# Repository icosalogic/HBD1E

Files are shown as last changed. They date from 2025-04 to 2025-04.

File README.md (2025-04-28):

# HBD1E
Kicad project for a configurable gate driver board to drive two MOSFETs with TO-247-4 package and
pinout [Drain, Source, KelvinSource, Gate].

Front side of board:

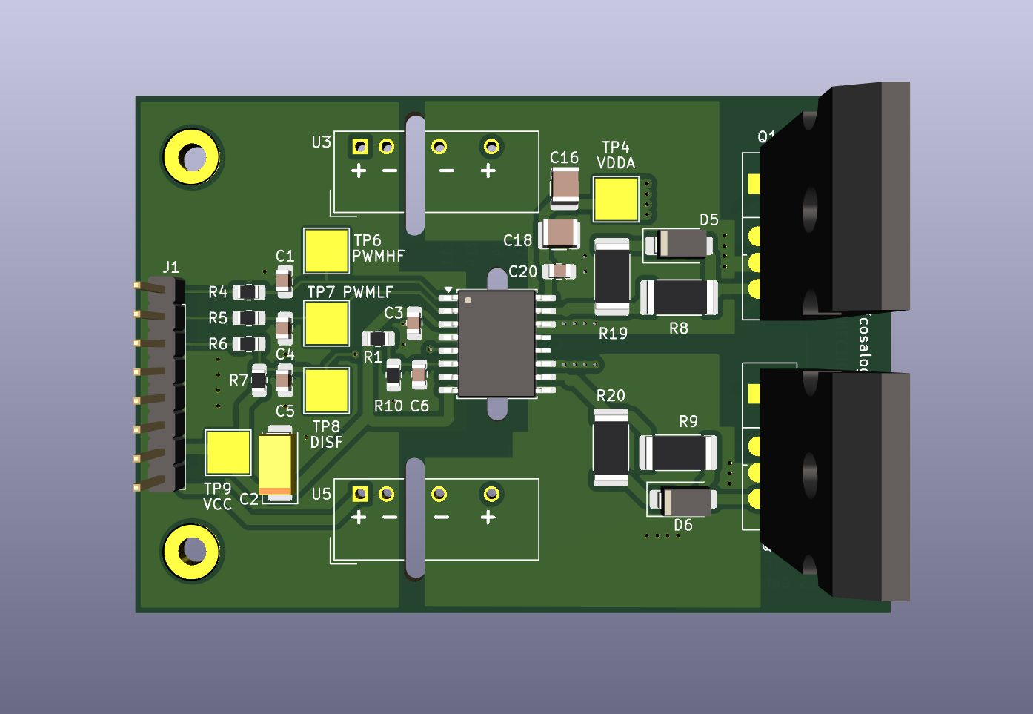
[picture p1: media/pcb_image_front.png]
Image front of PCB


Back side of board:

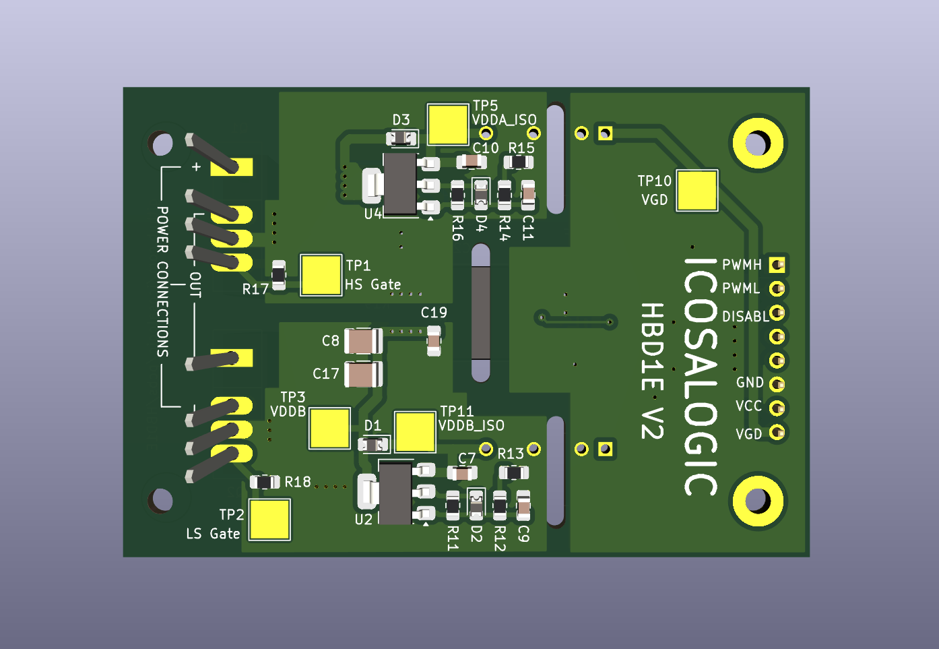
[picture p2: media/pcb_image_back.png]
Image back of PCB


# Features

- Supports 2 independent channels with 1 MOSFET per channel.
- No high-power connections on the board.  The user is free to connect the MOSFET power pins in any configuration they wish.
- Utilizes a gate driver chip in an SOIC-16 wide package, with a pin layout supported by multiple vendors.
- Each channel can be independently configured to be isolated from the gate driver control circuit.
- Each channel can be independently configured to use a linear regulator to precisely control the gate driver voltage.
- Most compatible gate driver chips support configurable dead time.

# Applications

- Half bridge, with input and output having a common ground: Configure the high side to be isolated, and the
low side non-isolated.
- T-Type inverter leg: Use 2 boards, with all gate power domains isolated, with the two middle MOSFETs configured
appropriately for common drain or common source.
- High power parallel MOSFETs: Disable dead time on the gate driver chip, and configure both MOSFET power
domains as non-isolated.

# Board Connections

Board input pins:  

Board input pins

- PWMH: PWM signal for the high-side MOSFET Q1, uses typical CMOS switching levels (off <= 0.8V, on >= 2.0V).
- PWML: PWM signal for the low-side MOSFET Q2, uses typical CMOS switching levels.
- DISABL: Pull this value low to enable the driver chip.  There is a pull up resistor to VCC on this circuit,
so the control component must pull this signal low to enable switching.  Uses typical CMOS switching levels.
- GND: Ground common to VCC and VGD.
- VCC: Power to the control side of the gate driver chip.  Typically 3.3V or 5V, maximum 20V.
- VGD: Power to the gate driver regions, optionally through isolation modules.

For the reference gate driver chip UCC21520, VCC and VGD may be the same for applications with lower
gate voltages.  Or you may choose to have them be separate, and use a higher voltage VGD to gain headroom
through the isolated modules, and configure the linear regulators to provide a precise post-isolation
gate drive voltage.

Note that there are no on-board connections for the high-current drain and source pins for either
MOSFET Q1 or Q2.  These must be connected separately, either through appropriately-sized wires or
a properly-designed laminated bus.

# Schematic

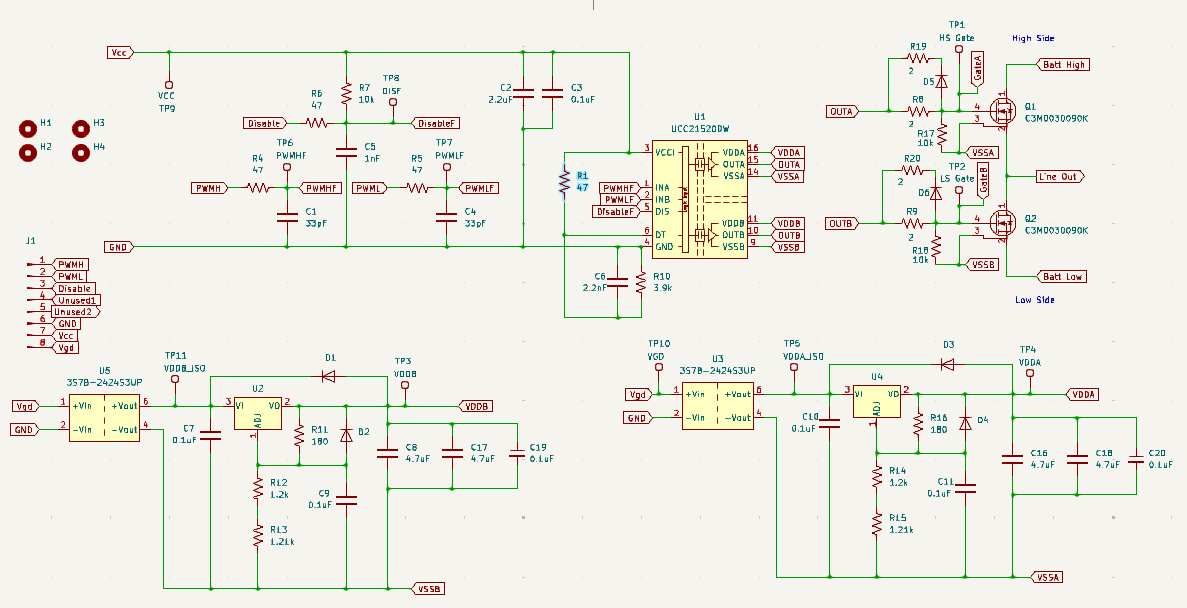
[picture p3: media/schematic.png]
Schematic drawing


# PCB Layout Details

PCB components:

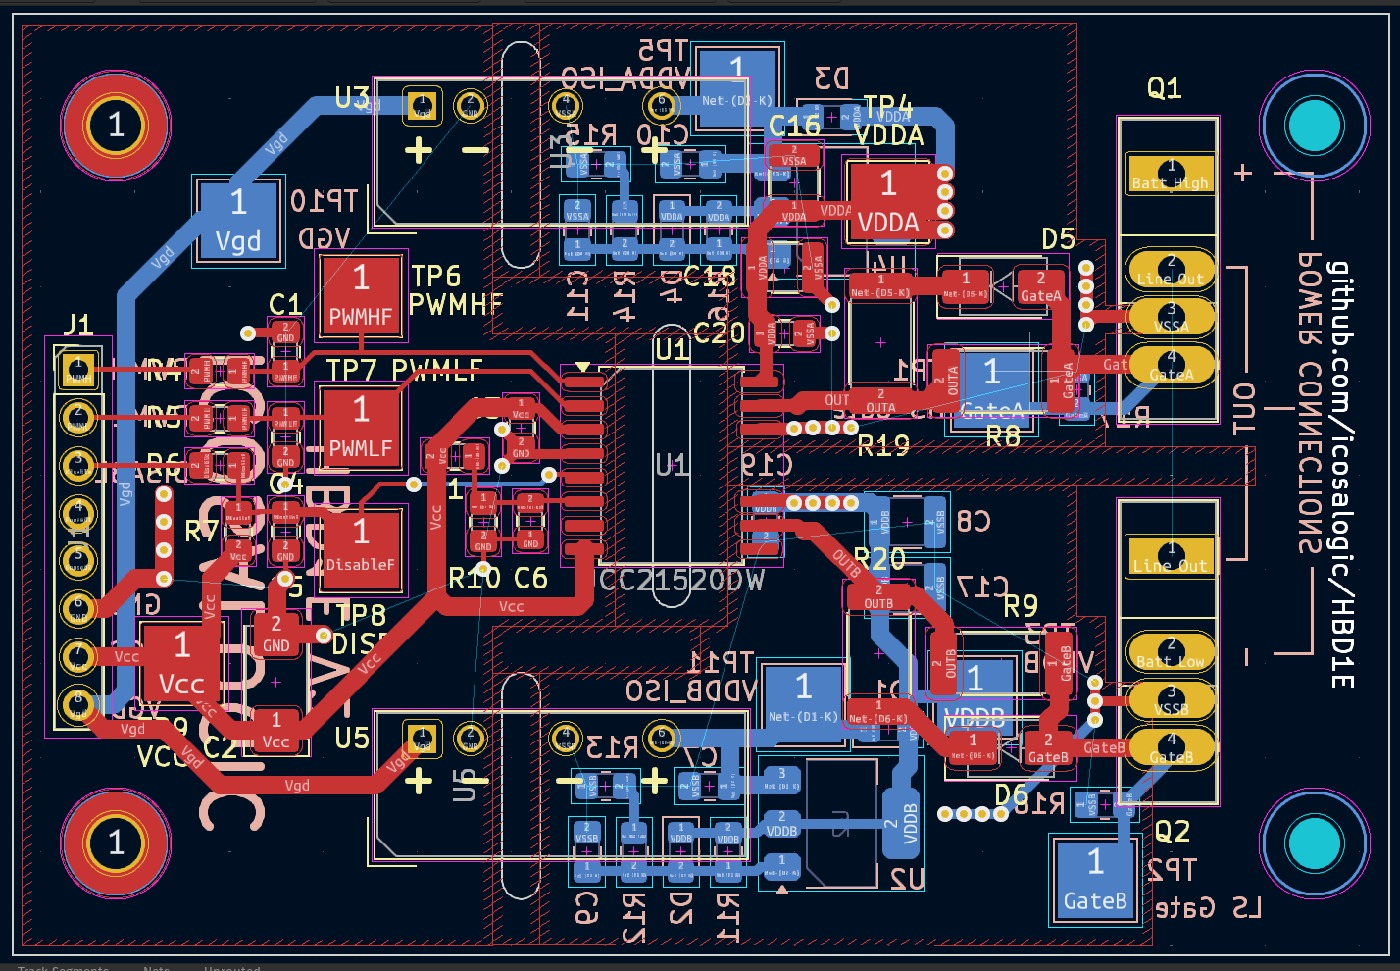
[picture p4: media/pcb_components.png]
PCB components


Front copper layer:

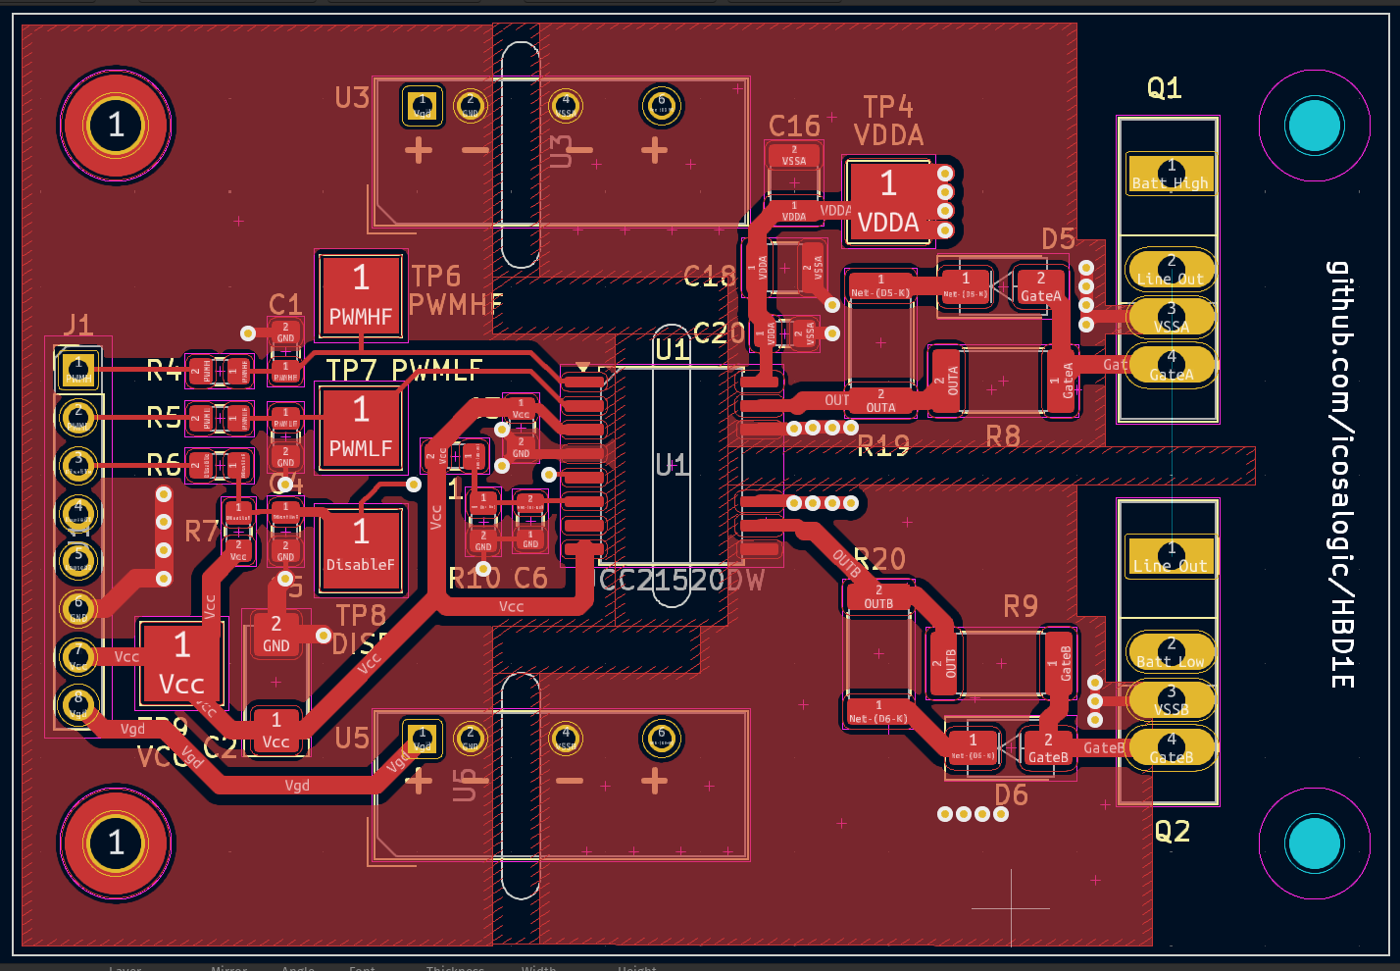
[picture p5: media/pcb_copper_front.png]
PCB front copper layer


Back copper layer:

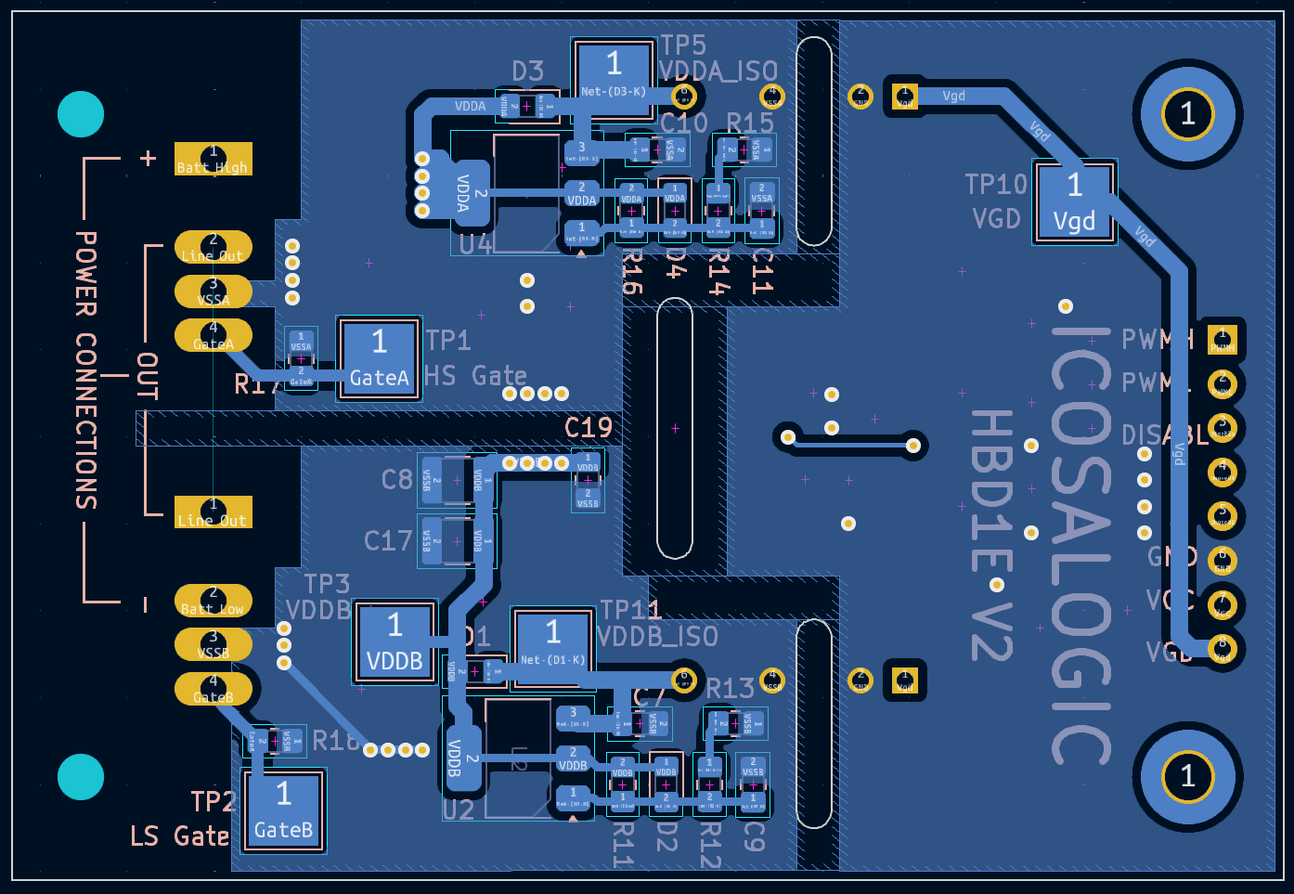
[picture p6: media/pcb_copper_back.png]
PCB back copper layer


# Configuring Channel Isolation

The front of the board has marked locations for two DC-DC isolated modules, U3 (high side, shown below) and U5 (low side).

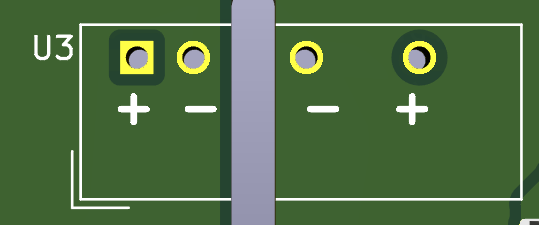
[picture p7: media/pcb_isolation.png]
Isolated module marking
  

These modules take power from the VGD pin, and supply it to the regions of the PCB driving the gates for
the high side MOSFET Q1 and the low side MOSFET Q2.

To make either region isolated, solder a DC-DC isolated converter module in the marked location.
Our test boards used a Gaptec 3S7B-2424S3UP, but pin-compatible 7-SIP components are available from multiple manufacturers.

To make one of these power domains non-isolated, solder a wire connection from + to + and another from - to -.
Ordinary AWG 20 gauge hookup wire is adequate.

# Configuring Gate Drive Voltage Regulation

On the back side of the board, under the isolated modules U3 and U5, are locations for LM317 linear regulators
and associated components.

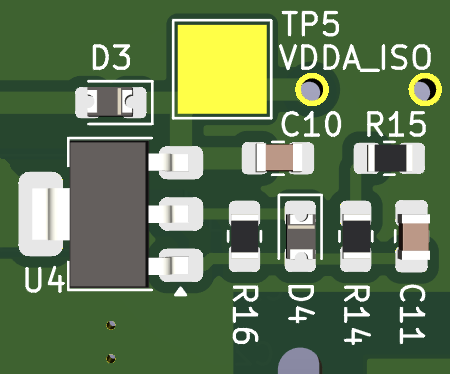
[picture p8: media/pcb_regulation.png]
Gate drive voltage regulation
  

- High Side: (under U3) U4, D3, D4, C10, C11, R14, R15, R16
- Low Side: (under U5) U2, D1, D2, C7, C9, R11, R12, R13

The following table shows which resistors on this board map to those in a typical LM317 datasheet.
This should allow you to select resistor values to configure your desired gate driver voltage.

| Datasheet | High Side | Low Side |
| --- | --- | --- |
| R1 | R16 | R11 |
| R2 |  R14+R15  | R12+R13  |

Note that we used 2 resistors in series for the R2 resistor from the datasheet.
The power dissipation from the minimum regulation current may exceed the limit for a typical
1/10 watt resistor, so we use 2 resistors in series to spread the thermal load.

Here is a table showing combinations for some typical gate drive voltages, using common resistor values.
Of course, more precise voltages can be obtained using more specific resistor values and higher
tolerance 0.1% resistors.

| Target Voltage | R16/R11 | R14+R15/R12+R13 | Computed Voltage |
| --- | --- | --- | --- |
| 10 | 180 | 270/1000 | 10.069 |
| 12 | 180 | 560/1000 | 12.083 |
| 15 | 180 | 1000/1000 | 15.139 |
| 18 | 180 | 1200/1200 | 17.917 |
| 20 | 180 | 1200/1500 | 20.000 |

Note also that the LM317 is a very robust device that may not require all the configured components.
The adjust capacitors may be omitted if your testing shows that ripple and other voltage transients
do not cause any downstream issues when switching the MOSFETs.
Each of the adjust capacitors is paired with a diode:

- C9, D2
- C11, D4

If you omit the adjust capacitor, you can also omit the matching diode.  If you use the adjust capacitor,
you should also use the diode to prevent the capacitor from discharging through the regulator in a power off
scenario.

Also note that you should always populate D1 and D3, since there are large capacitors for the gate driver
chip that may discharge through the regulator in a power off scenario.  D1 and D3 will prevent this.

To configure either the high-side or low-side power domain for voltage regulation, populate the associated
components as listed above.

To configure either of the power domains without voltage regulation, omit all of the regulation components
listed above for that domain, and replace the associated diode (D1 or D3) with a 0 ohm shunt resistor.

# Configuring Dead Time

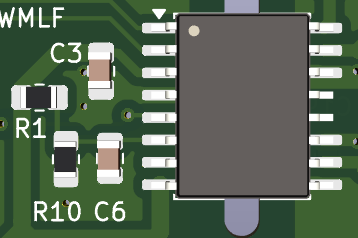
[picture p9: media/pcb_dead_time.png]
Dead time configuration
  

The components used to configure dead time are R1, R10 and C6.

Some, but not all of the pin-compatible gate driver chips support controlling dead time between Q1 and Q2
gate transitions, using a resistor connected to pin 6.  If the gate driver chip you use does not support dead
time generation, then do not populate R1, R10 and C6, and ignore the rest of this section.

If your gate driver chip supports dead time insertion, populate R10 and optionally C6 according to the
datasheet for your chip.  Do not populate R1.

If your chip supports dead time insertion, but you wish to suppress it, populate R1, but not R10 and C6.
This may be desireable if you use this board in a high-current parallel MOSFET application, where you want
both MOSFETs on at the same time.

If your control logic providing the PWM signals also implements dead time, one strategy is to program an
absolute minimum dead time via the hardware as described in this section, and program an optimized, longer
dead time in your control logic.  The gate driver chip uses the longer of the hardware configured dead
time or the software-controlled dead time in the PWM inputs.

# Configuring Input Signal Filtering

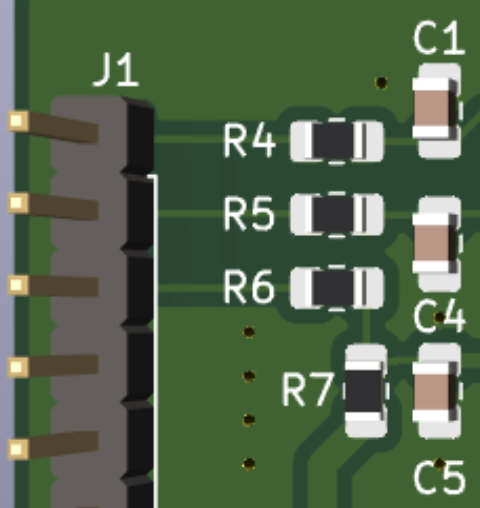
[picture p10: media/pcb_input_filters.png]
Input signal filter configuration


Each of the 3 input signals from the controller to this gate driver board has an RC circuit to
filter transients that may cause issues for the gate driver IC input logic.  These signals and the
associated filter components are listed below.

| Signal Name | Filter Resistor | Value | Capacitor | Value | Pull Up Resistor | Value |
| --- | --- | ----- | --- | ----- | --- | ----- |
| PWMH | R4 |  47Ω | C1 |  33pF | | |
| PWML | R5 |  47Ω | C4 |  33pF | | |
| DISABL | R6 |  47Ω | C5 | 1nF | R7 |  10k  |

The size of all these components is 0805, making them less trouble to hand solder while changing
filter components.

# Test Points

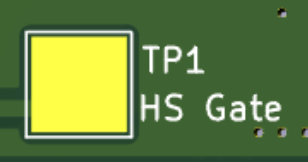
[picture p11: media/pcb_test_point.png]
Test points


There are numerous test points located on both sides of the board to which users can solder
surface mount test point loops, for example KOA Speer RCWCTE.
This gives you the ability to clip oscilloscope leads to enable monitoring various signals while
debugging the gate driver configuration.

### Caution!  This board may use high voltages that are hazardous to humans.
- Be very careful when connecting test leads to potentially high voltage points on the circuit board.
- High voltages may also break test equipment if proper grounding and isolation practices are not followed.
- Please be careful!

List of test points on the board:
| Label |  Name | Location | Description |
| ----- | --- | --- | --- |
| TP1 | HS Gate  | Bottom | High side MOSFET gate pin |
| TP2 | LS Gate  | Bottom | Low side MOSFET gate pin |
| TP3 | VDDB | Bottom | Low side post-regulated gate driver voltage |
| TP4 | VDDA | Top | High side post-regulated gate driver voltage |
| TP5 | VDDA_ISO | Bottom | High side post-isolation, pre-regulated voltage |
| TP6 | PWMHF | Top | High side post-filter PWM input signal |
| TP7 | PWMLF | Top | Low side post-filter PWM input signal |
| TP8 | DISF | Top | Disable post-filter input signal |
| TP9 | VCC | Top | Logic side power for gate driver chip |
| TP10  | VGD | Bottom | Pre-isolation gate driver voltage |
| TP11  | VDDB_ISO | Bottom | Low side post-isolation, pre-regulated voltage  |

# Reference Components

- Gate driver chip: Texas Instruments UCC21520
- MOSFET: Infineon AIMZH120R020M1TXKSA1
- Isolated DC-DC module: Gaptec 3S7B-2424S3UP
- Linear Regulator: Texas Instruments LM317

# Example Bill of Materials (BOM)

An example BOM is located in the file HBD1E_BOM.csv.

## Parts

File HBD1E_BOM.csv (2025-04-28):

Id | Designator | Footprint | Quantity | Designation | Supplier and ref
1 | TP4 | TestPoint_Pad_4.0x4.0mm | 1 | VDDA
2 | H2,H1 | MountingHole_2.7mm_M2.5_Pad_TopBottom | 2 | MountingHole
3 | Q1,Q2 | TO-247-4_Vertical | 2 | C3M0030090K
4 | C5 | C_0805_2012Metric_Pad1.18x1.45mm_HandSolder | 1 | 1nF
5 | C2 | CP_EIA-6032-20_AVX-F_Pad2.25x2.35mm_HandSolder | 1 | 2.2uF
6 | R6,R5,R1,R4 | R_0805_2012Metric_Pad1.20x1.40mm_HandSolder | 4 | 47
7 | D5,D6 | D_SMA | 2 | US1B
8 | TP9 | TestPoint_Pad_4.0x4.0mm | 1 | VCC
9 | TP6 | TestPoint_Pad_4.0x4.0mm | 1 | PWMHF
10 | R9,R19,R20,R8 | R_2512_6332Metric_Pad1.40x3.35mm_HandSolder | 4 | 2
11 | TP7 | TestPoint_Pad_4.0x4.0mm | 1 | PWMLF
12 | C1,C4 | C_0805_2012Metric_Pad1.18x1.45mm_HandSolder | 2 | 33pF
13 | C6 | C_0805_2012Metric | 1 | 2.2nF
14 | U5,U3 | Converter_DCDC_TRACO_TBA2-xxxx_Single_THT | 2 | 3S7B-2424S3UP
15 | R10 | R_0805_2012Metric_Pad1.20x1.40mm_HandSolder | 1 | 3.9k
16 | C3,C20,C9,C10,C7,C19,C11 | C_0805_2012Metric_Pad1.18x1.45mm_HandSolder | 7 | 0.1uF
17 | C16,C18,C17,C8 | C_1210_3225Metric | 4 | 4.7uF
18 | H4,H3 | MountingHole_2.7mm | 2 | MountingHole
19 | J1 | PinHeader_1x08_P2.54mm_Vertical | 1 | Conn_01x08_Male
20 | U1 | SOIC-16W_7.5x10.3mm_P1.27mm_no_pins_12_13 | 1 | UCC21520DW
21 | R7,R17,R18 | R_0805_2012Metric_Pad1.20x1.40mm_HandSolder | 3 | 10k
22 | TP8 | TestPoint_Pad_4.0x4.0mm | 1 | DISF
23 | TP2 | TestPoint_Pad_4.0x4.0mm | 1 | LS Gate
24 | TP1 | TestPoint_Pad_4.0x4.0mm | 1 | HS Gate
25 | R11,R16 | R_0805_2012Metric_Pad1.20x1.40mm_HandSolder | 2 | 180
26 | R14,R12 | R_0805_2012Metric_Pad1.20x1.40mm_HandSolder | 2 | 1.2k
27 | R13,R15 | R_0805_2012Metric_Pad1.20x1.40mm_HandSolder | 2 | 1.21k
28 | U2,U4 | SOT-223-3_TabPin2 | 2 | LM317_SOT-223
29 | D4,D1,D3,D2 | D_0805_2012Metric_Pad1.15x1.40mm_HandSolder | 4 | US1B
30 | TP10 | TestPoint_Pad_4.0x4.0mm | 1 | VGD
31 | TP5 | TestPoint_Pad_4.0x4.0mm | 1 | VDDA_ISO
32 | TP3 | TestPoint_Pad_4.0x4.0mm | 1 | VDDB
33 | TP11 | TestPoint_Pad_4.0x4.0mm | 1 | VDDB_ISO

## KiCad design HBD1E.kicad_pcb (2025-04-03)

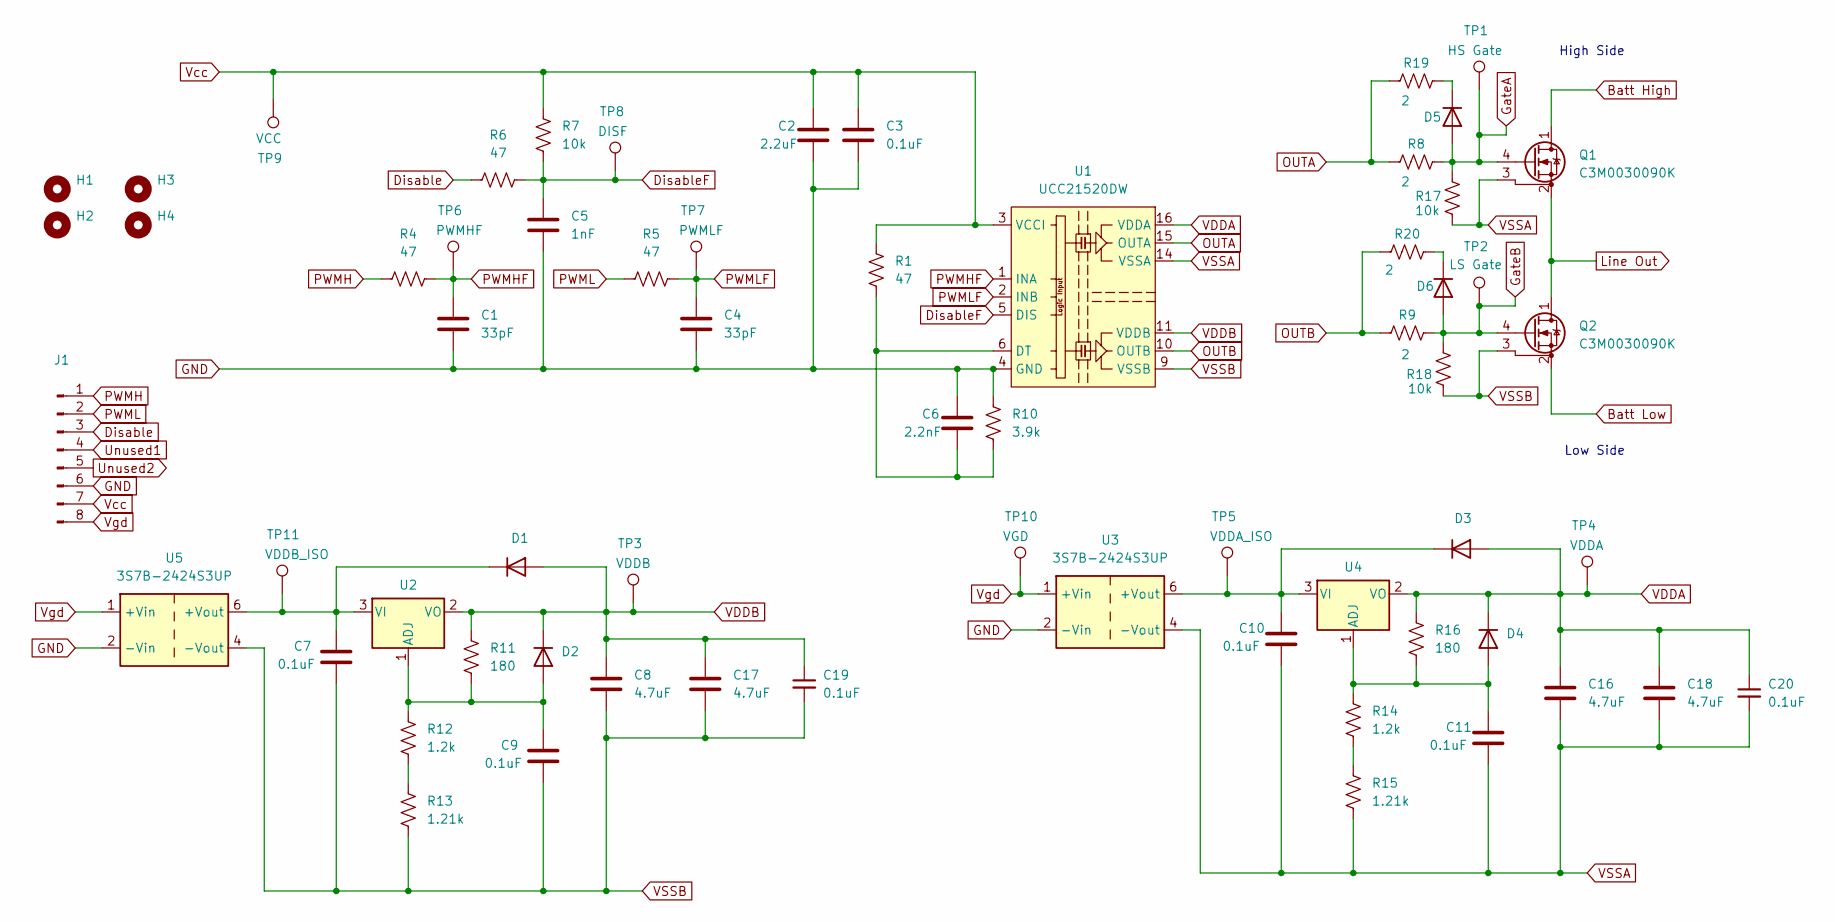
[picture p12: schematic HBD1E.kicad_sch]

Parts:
C1, C4: 33pF; C_0805_2012Metric_Pad1.18x1.45mm_HandSolder
C2: 2.2uF; CP_EIA-6032-20_AVX-F_Pad2.25x2.35mm_HandSolder
C3, C7, C9, C10, C11, C19, C20: 0.1uF; C_0805_2012Metric_Pad1.18x1.45mm_HandSolder
C5: 1nF; C_0805_2012Metric_Pad1.18x1.45mm_HandSolder
C6: 2.2nF; C_0805_2012Metric
C8, C16, C17, C18: 4.7uF; C_1210_3225Metric
D1, D2, D3, D4: US1B; D_0805_2012Metric_Pad1.15x1.40mm_HandSolder
D5, D6: US1B; D_SMA
H1, H2: MountingHole; MountingHole_2.7mm_M2.5_Pad_TopBottom
H3, H4: MountingHole; MountingHole_2.7mm
J1: Conn_01x08_Male; PinHeader_1x08_P2.54mm_Vertical
Q1, Q2: C3M0030090K; TO-247-4_Vertical
R1, R4, R5, R6: 47; R_0805_2012Metric_Pad1.20x1.40mm_HandSolder
R7, R17, R18: 10k; R_0805_2012Metric_Pad1.20x1.40mm_HandSolder
R8, R9, R19, R20: 2; R_2512_6332Metric_Pad1.40x3.35mm_HandSolder
R10: 3.9k; R_0805_2012Metric_Pad1.20x1.40mm_HandSolder
R11, R16: 180; R_0805_2012Metric_Pad1.20x1.40mm_HandSolder
R12, R14: 1.2k; R_0805_2012Metric_Pad1.20x1.40mm_HandSolder
R13, R15: 1.21k; R_0805_2012Metric_Pad1.20x1.40mm_HandSolder
TP1: HS Gate; TestPoint_Pad_4.0x4.0mm
TP2: LS Gate; TestPoint_Pad_4.0x4.0mm
TP3: VDDB; TestPoint_Pad_4.0x4.0mm
TP4: VDDA; TestPoint_Pad_4.0x4.0mm
TP5: VDDA_ISO; TestPoint_Pad_4.0x4.0mm
TP6: PWMHF; TestPoint_Pad_4.0x4.0mm
TP7: PWMLF; TestPoint_Pad_4.0x4.0mm
TP8: DISF; TestPoint_Pad_4.0x4.0mm
TP9: VCC; TestPoint_Pad_4.0x4.0mm
TP10: VGD; TestPoint_Pad_4.0x4.0mm
TP11: VDDB_ISO; TestPoint_Pad_4.0x4.0mm
U1: UCC21520DW; SOIC-16W_7.5x10.3mm_P1.27mm_no_pins_12_13
U2, U4: LM317_SOT-223; SOT-223-3_TabPin2
U3, U5: 3S7B-2424S3UP; Converter_DCDC_TRACO_TBA2-xxxx_Single_THT

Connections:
Batt High: Q1.1 (D)
Batt Low: Q2.2 (S)
Disable: J1.3, R6.2
DisableF: C5.1, R6.1, R7.1, TP8.1, U1.5 (DIS)
GND: C1.2, C2.2, C3.2, C4.2, C5.2, C6.1, J1.6, R10.2, U1.4 (GND), U3.2 (-Vin), U5.2 (-Vin)
GateA: D5.2 (A), Q1.4 (G), R8.1, R17.2, TP1.1
GateB: D6.2 (A), Q2.4 (G), R9.1, R18.2, TP2.1
Line Out: Q1.2 (S), Q2.1 (D)
unnamed: C7.1, D1.1 (K), TP11.1, U2.3 (VI), U5.6 (+Vout)
unnamed: C9.1, D2.2 (A), R11.1, R12.2, U2.1 (ADJ)
unnamed: C10.1, D3.1 (K), TP5.1, U3.6 (+Vout), U4.3 (VI)
unnamed: C11.1, D4.2 (A), R14.2, R16.1, U4.1 (ADJ)
unnamed: D5.1 (K), R19.1
unnamed: D6.1 (K), R20.1
unnamed: R12.1, R13.2
unnamed: R14.1, R15.2
unnamed: C6.2, R1.1, R10.1, U1.6 (DT)
OUTA: R8.2, R19.2, U1.15 (OUTA)
OUTB: R9.2, R20.2, U1.10 (OUTB)
PWMH: J1.1, R4.2
PWMHF: C1.1, R4.1, TP6.1, U1.1 (INA)
PWML: J1.2, R5.2
PWMLF: C4.1, R5.1, TP7.1, U1.2 (INB)
Unused1: J1.4
Unused2: J1.5
VDDA: C16.1, C18.1, C20.1, D3.2 (A), D4.1 (K), R16.2, TP4.1, U1.16 (VDDA), U4.2 (VO)
VDDB: C8.1, C17.1, C19.1, D1.2 (A), D2.1 (K), R11.2, TP3.1, U1.11 (VDDB), U2.2 (VO)
VSSA: C10.2, C11.2, C16.2, C18.2, C20.2, Q1.3 (DS), R15.1, R17.1, U1.14 (VSSA), U3.4 (-Vout)
VSSB: C7.2, C8.2, C9.2, C17.2, C19.2, Q2.3 (DS), R13.1, R18.1, U1.9 (VSSB), U5.4 (-Vout)
Vcc: C2.1, C3.1, J1.7, R1.2, R7.2, TP9.1, U1.3 (VCCI), U1.8 (VCCI)
Vgd: J1.8, TP10.1, U3.1 (+Vin), U5.1 (+Vin)

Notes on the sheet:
High Side
Low Side

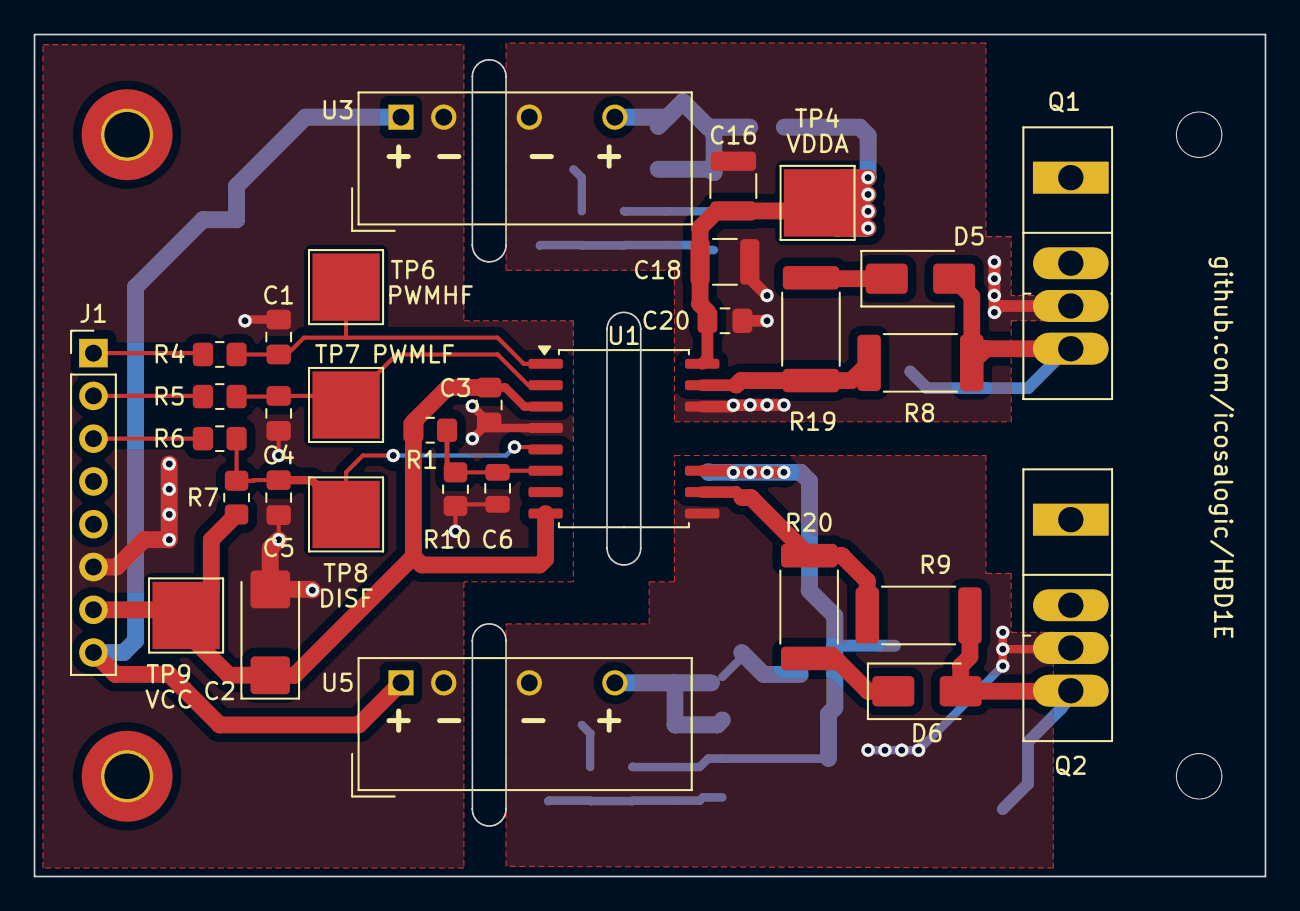
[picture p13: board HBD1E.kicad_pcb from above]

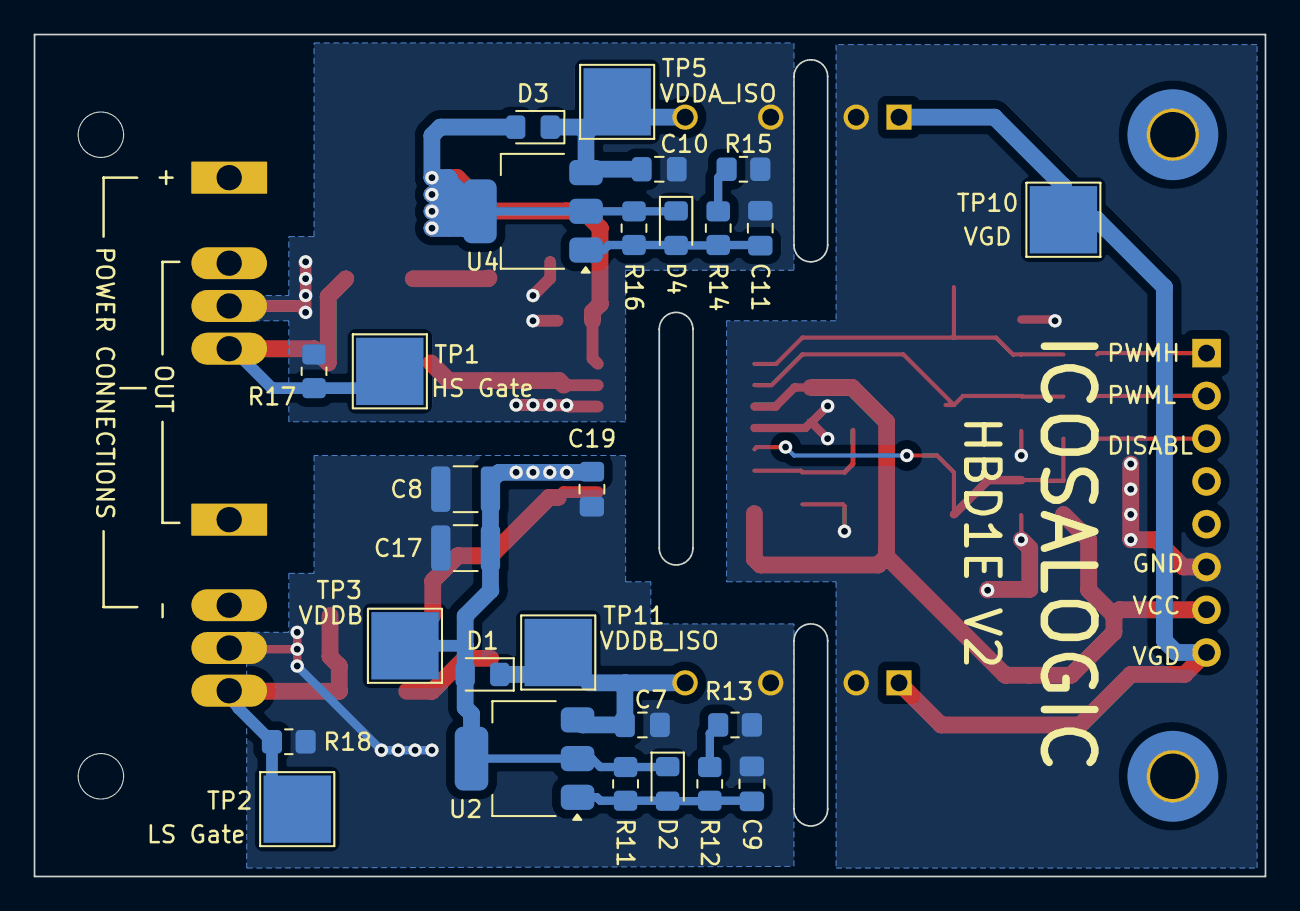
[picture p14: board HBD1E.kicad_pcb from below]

Board: 2 copper layers, 73.1 x 50.0 mm, 63 parts (27 on the bottom side), 27 nets.

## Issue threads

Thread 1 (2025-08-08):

Put all test points on the top side

icosalogic, 2025-08-08:
This board doesn't have the high-voltage, high-current circuits on the board, so there will be either large wires or a laminated bus bar on the bottom side of the board where the MOSFET pins can reach them.

Also, to minimize the path length from the DC link capacitor through the MOSFET to the output inductor, the DC link capacitor will also often be directly under the board.

As a result, the test points on the bottom side of the board are unusable in a real-world configuration.

Here is an image the illustrates the problem.

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

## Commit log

2025-04-02 Initial checkin.
    [HBD1E.kicad_pcb, HBD1E.kicad_sch]
2025-04-02 Initial checkin of gerber files.
    [HBD1E-B_Cu.gbl, HBD1E-B_Mask.gbs, HBD1E-B_Paste.gbp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]
2025-04-03 First check in of board image files.
2025-04-03 Added a pull-up resistor for dead time configuration.
    [HBD1E-B_Cu.gbl, HBD1E-B_Mask.gbs, HBD1E-B_Paste.gbp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]
2025-04-03 Added a table to README describing which resistors determine linear regulator output voltage.
2025-04-03 Fixed incorrect project location in PCB text object.
    [HBD1E.kicad_pcb]
2025-04-26 Updated README for input filters and test points. Changed name in license file.
2025-04-28 Added a BOM file and updated README with possible LM317 resistor combinations for typical gate drive voltages.
    [HBD1E_BOM.csv]
